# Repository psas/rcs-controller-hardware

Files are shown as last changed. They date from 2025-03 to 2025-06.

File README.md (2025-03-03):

# rcs-controller-hardware
The controller PCB for the RCS v2 module

Design documentation can be found [here](https://docs.google.com/document/d/1iXMG_Qmra7nCvFc8n4LBztUYELcxyuHCIxhkm7w4VaU/edit?usp=sharing).
## LICENSE

Copyright the Portland State Aerospace Society, 2025.

This source describes Open Hardware that is licensed under CERN-OHL-S v2, or any later version.

You may redistribute and modify this source and make products using it under the terms of the CERN-OHL-S v2 (https://ohwr.org/cern_ohl_s_v2.txt).

This source is distributed WITHOUT ANY EXPRESS OR IMPLIED WARRANTY, INCLUDING OF MERCHANTABILITY, SATISFACTORY QUALITY AND FITNESS FOR A PARTICULAR PURPOSE. Please see the CERN-OHL-S v2 for applicable conditions.

Source location: https://github.com/psas/

If you require a different license for this open hardware project, please contact us at [aerospace@pdx.edu](mailto:aerospace@pdx.edu).

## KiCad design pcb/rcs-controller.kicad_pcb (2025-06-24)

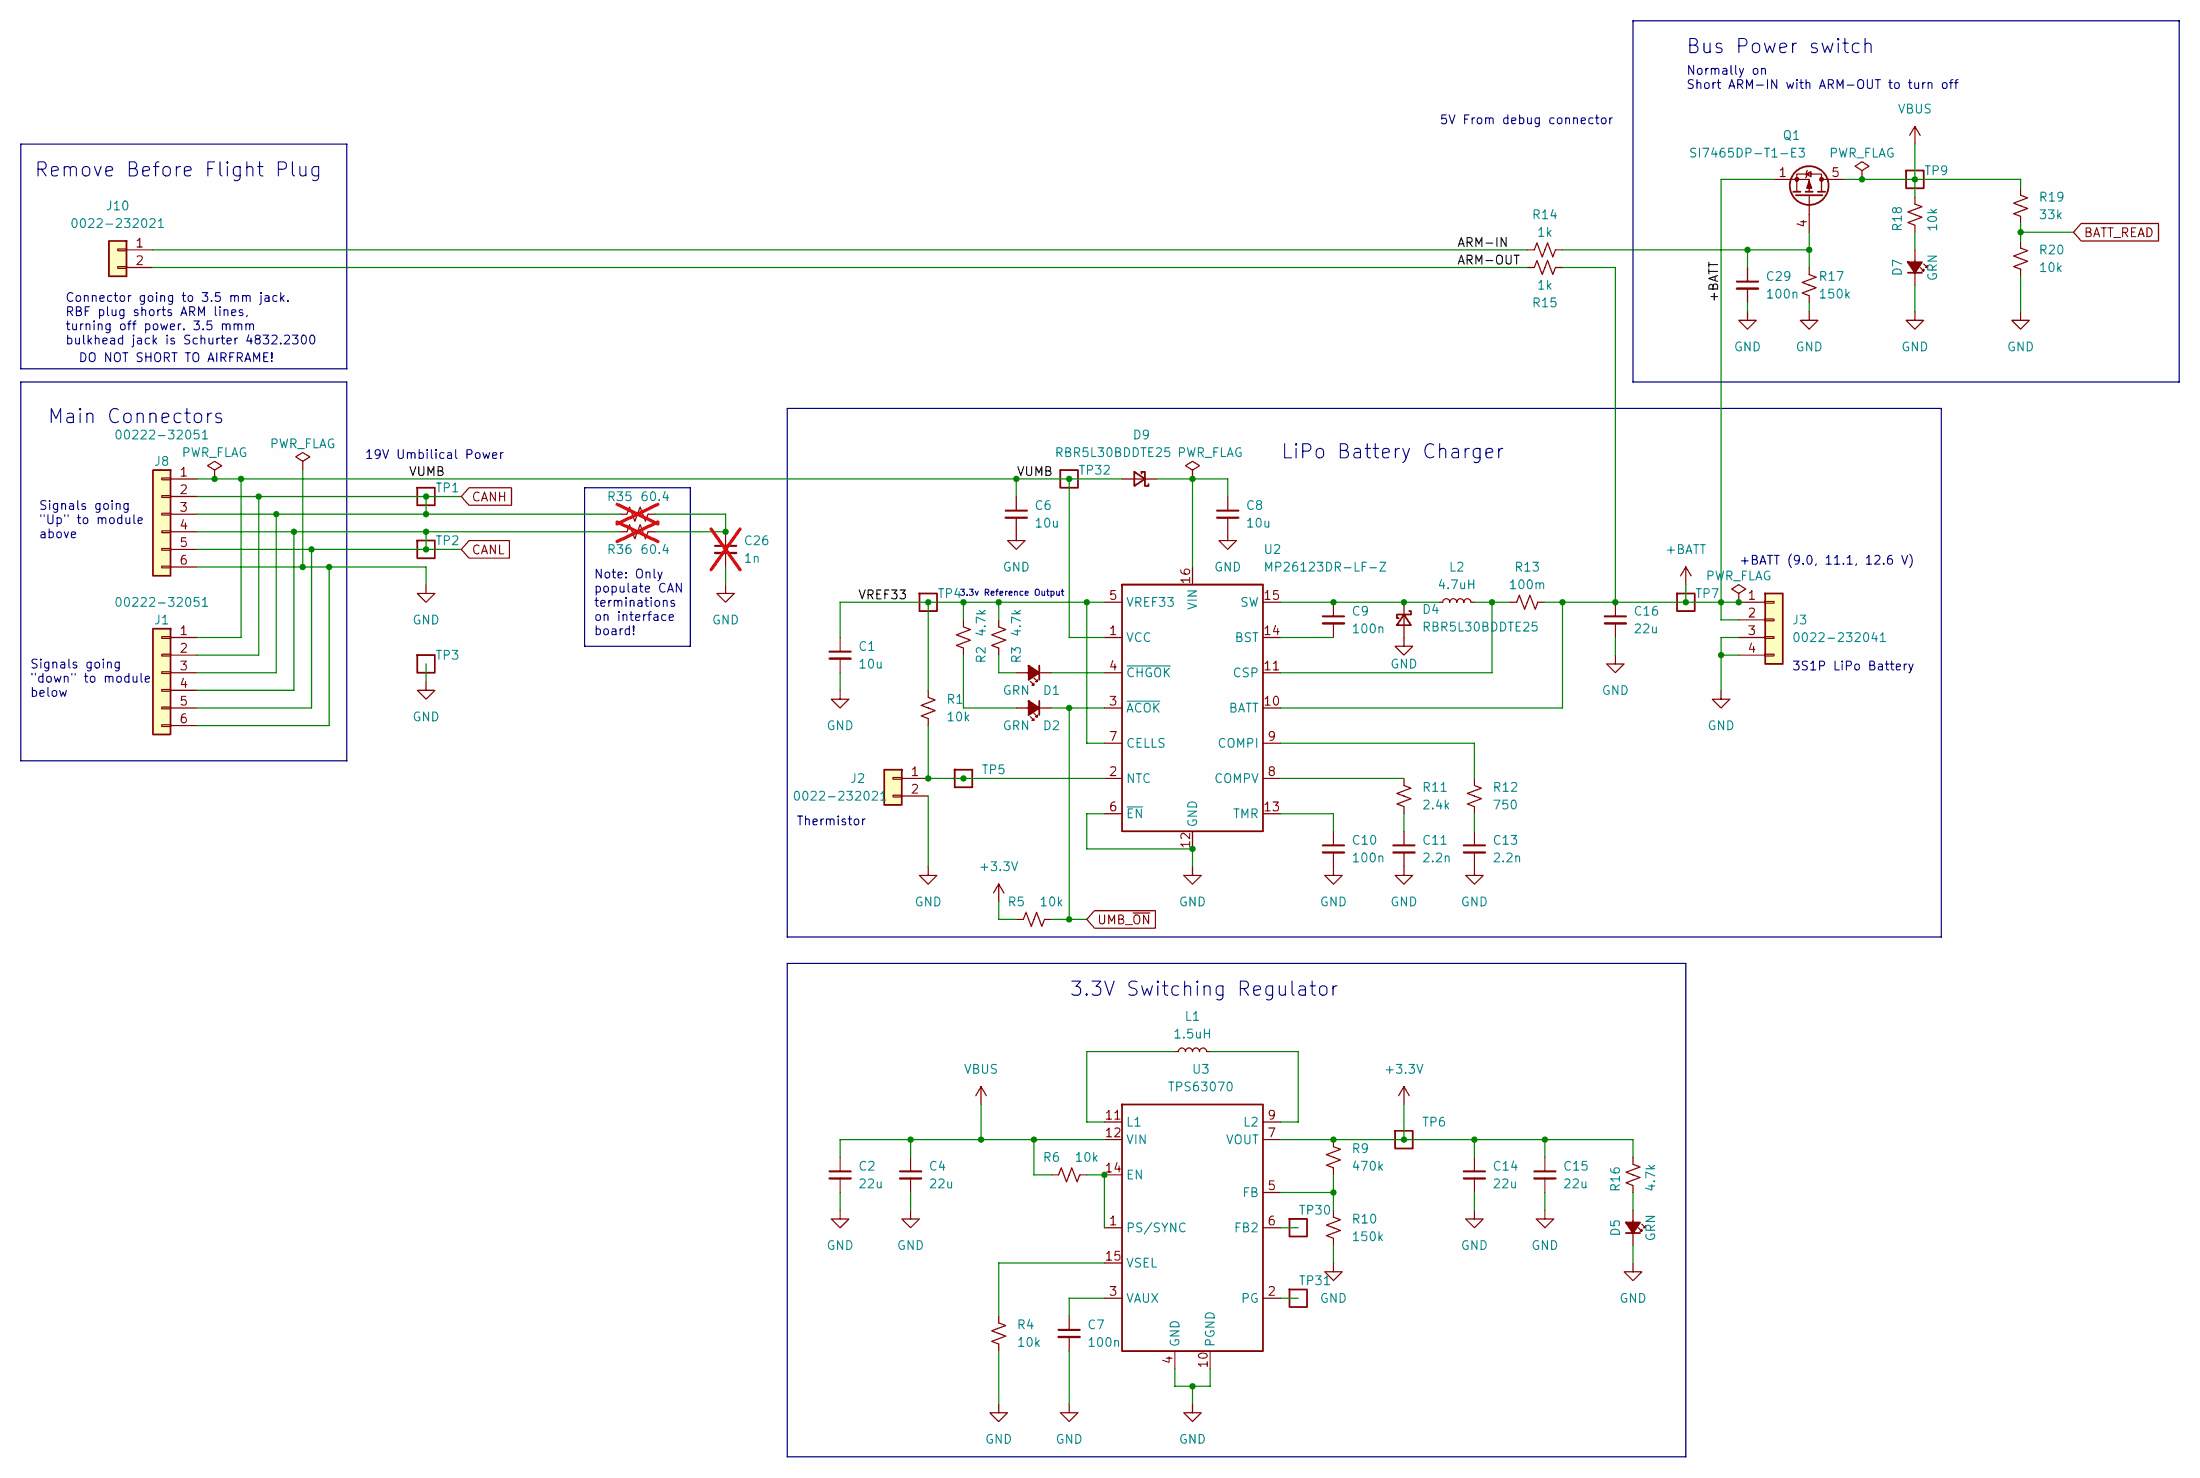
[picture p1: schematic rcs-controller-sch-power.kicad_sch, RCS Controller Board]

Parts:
C1, C6, C8: 10u; C_0805_2012Metric; MPN GRM21BR61H106KE43L
C2, C4, C14, C15, C16: 22u; C_0805_2012Metric; MPN C2012X5R1V226M125AC
C7, C9, C10, C29: 100n; C_0603_1608Metric; MPN CL10B104KB8WPNC
C11, C13: 2.2n; C_0603_1608Metric; MPN CL10B222KB8WPNC
C26: 1n; C_0603_1608Metric; MPN CL10B102KB85PNL; not fitted
D1, D2, D5, D7: GRN; LED_0603_1608Metric; MPN 150060GS75000
D4, D9: RBR5L30BDDTE25; D_SMA; MPN RBR5L30BDDTE25
J1, J8: 00222-32051; Molex_KK-254_AE-6410-06A_1x06_P2.54mm_Vertical; MPN 22232061
J2, J10: 0022-232021; Molex_KK-254_AE-6410-02A_1x02_P2.54mm_Vertical; MPN 22232021
J3: 0022-232041; Molex_KK-254_AE-6410-04A_1x04_P2.54mm_Vertical; MPN 22232041
L1: 1.5uH; L_Vishay_IHLP-2020; MPN IHLP2020CZER1R5M11
L2: 4.7uH; L_Vishay_IHLP-2020; MPN IHLP2020BZER4R7M11
Q1: SI7465DP-T1-E3; PowerPAK_SO-8_Single; MPN SI7141DP-T1-GE3
R1, R4, R5, R6, R18, R20: 10k; R_0603_1608Metric; MPN RC0603FR-0710KL
R2, R3, R16: 4.7k; R_0603_1608Metric; MPN RC0603FR-074K7L
R9: 470k; R_0603_1608Metric; MPN RC0603FR-07470KL
R10, R17: 150k; R_0603_1608Metric; MPN RC0603FR-07150KL
R11: 2.4k; R_0603_1608Metric; MPN RC0603FR-072K4L
R12: 750; R_0603_1608Metric; MPN RC0603FR-07750RL
R13: 100m; R_1206_3216Metric; MPN CSR1206FTR100
R14, R15: 1k; R_0603_1608Metric; MPN RC0603FR-071KL
R19: 33k; R_0603_1608Metric; MPN RC0603FR-0733KL
R35, R36: 60.4; R_1206_3216Metric; MPN RC0603FR-0760R4L; not fitted
TP1, TP2, TP3, TP4, TP5, TP6, TP7, TP9, TP30, TP31, TP32: Test-Point; TP-through-hole-1X01
U2: MP26123DR-LF-Z; QFN-16-1EP_4x4mm_P0.65mm_EP2.5x2.5mm; MPN MP26123DR-LF-Z
U3: TPS63070; U-TI-TPS63070; MPN TPS63070RNMR

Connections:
+3.3V: C14.1, C15.1, R5.1, R9.1, R16.1, TP6.1, U3.7 (VOUT), U3.8 (VOUT), U3.TIE2 (VOUT); also elsewhere on the board
+BATT: C16.1, J3.1, J3.2, Q1.1 (S), Q1.2 (S), Q1.3 (S), R13.2, R15.1, TP7.1, U2.10 (BATT)
/Power/ARM-IN: J10.1, R14.1
/Power/ARM-OUT: J10.2, R15.2
/Power/VREF33: C1.1, R1.1, R2.1, R3.1, TP4.1, U2.5 (VREF33), U2.7 (CELLS)
/Power/VUMB: C6.1, D9.2 (A), J1.1, J8.1, TP32.1, U2.1 (VCC)
BATT_READ: R19.2, R20.1; also elsewhere on the board
CANH: J1.2, J1.3, J8.2, J8.3, R35.1, TP1.1
CANL: J1.4, J1.5, J8.4, J8.5, R36.2, TP2.1
GND: C1.2, C2.2, C4.2, C6.2, C7.2, C8.2, C10.2, C11.2, C13.2, C14.2, C15.2, C16.2, C26.2, C29.2, D4.2 (A), D5.1 (K), D7.1 (K), J1.6, J2.2, J3.3, J3.4, J8.6, R4.2, R10.2, R17.2, R20.2, TP3.1, U2.6 (~EN), U2.12 (GND), U2.17 (GND), U3.4 (GND), U3.10 (PGND); also elsewhere on the board
unnamed: C11.1, R11.2
unnamed: C13.1, R12.2
unnamed: C26.1, R35.2, R36.1
unnamed: D1.2 (A), R3.2
unnamed: D1.1 (K), U2.4 (~CHGOK)
unnamed: D2.2 (A), R2.2
unnamed: C9.1, D4.1 (K), L2.1, U2.15 (SW)
unnamed: D5.2 (A), R16.2
unnamed: D7.2 (A), R18.2
unnamed: C8.1, D9.1 (K), U2.16 (VIN)
unnamed: J2.1, R1.2, TP5.1, U2.2 (NTC)
unnamed: C29.1, Q1.4 (G), R14.2, R17.1
unnamed: C9.2, U2.14 (BST)
unnamed: R12.1, U2.9 (COMPI)
unnamed: R11.1, U2.8 (COMPV)
unnamed: L2.2, R13.1, U2.11 (CSP)
unnamed: C10.1, U2.13 (TMR)
unnamed: R6.2, U3.1 (PS/SYNC), U3.14 (EN)
unnamed: TP30.1, U3.6 (FB2)
unnamed: R9.2, R10.1, U3.5 (FB)
unnamed: L1.1, U3.11 (L1)
unnamed: L1.2, U3.9 (L2)
unnamed: TP31.1, U3.2 (PG)
unnamed: C7.1, U3.3 (VAUX)
unnamed: R4.1, U3.15 (VSEL)
UMB_~ON: D2.1 (K), R5.2, U2.3 (~ACOK); also elsewhere on the board
VBUS: C2.1, C4.1, Q1.5 (D), R6.1, R18.1, R19.1, TP9.1, U3.12 (VIN), U3.13 (VIN), U3.TIE1 (VIN); also elsewhere on the board

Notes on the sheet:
LiPo Battery Charger
DO NOT SHORT TO AIRFRAME!
Thermistor
Signals going "down" to module below
Normally on Short ARM-IN with ARM-OUT to turn off
Connector going to 3.5 mm jack. RBF plug shorts ARM lines, turning off power. 3.5 mmm bulkhead jack is Schurter 4832.2300
Note: Only populate CAN terminations on interface board!
3S1P LiPo Battery
Signals going "Up" to module above
19V Umbilical Power
+BATT (9.0, 11.1, 12.6 V)
Bus Power switch
Main Connectors
3.3V Switching Regulator
5V From debug connector
3.3v Reference Output
Remove Before Flight Plug

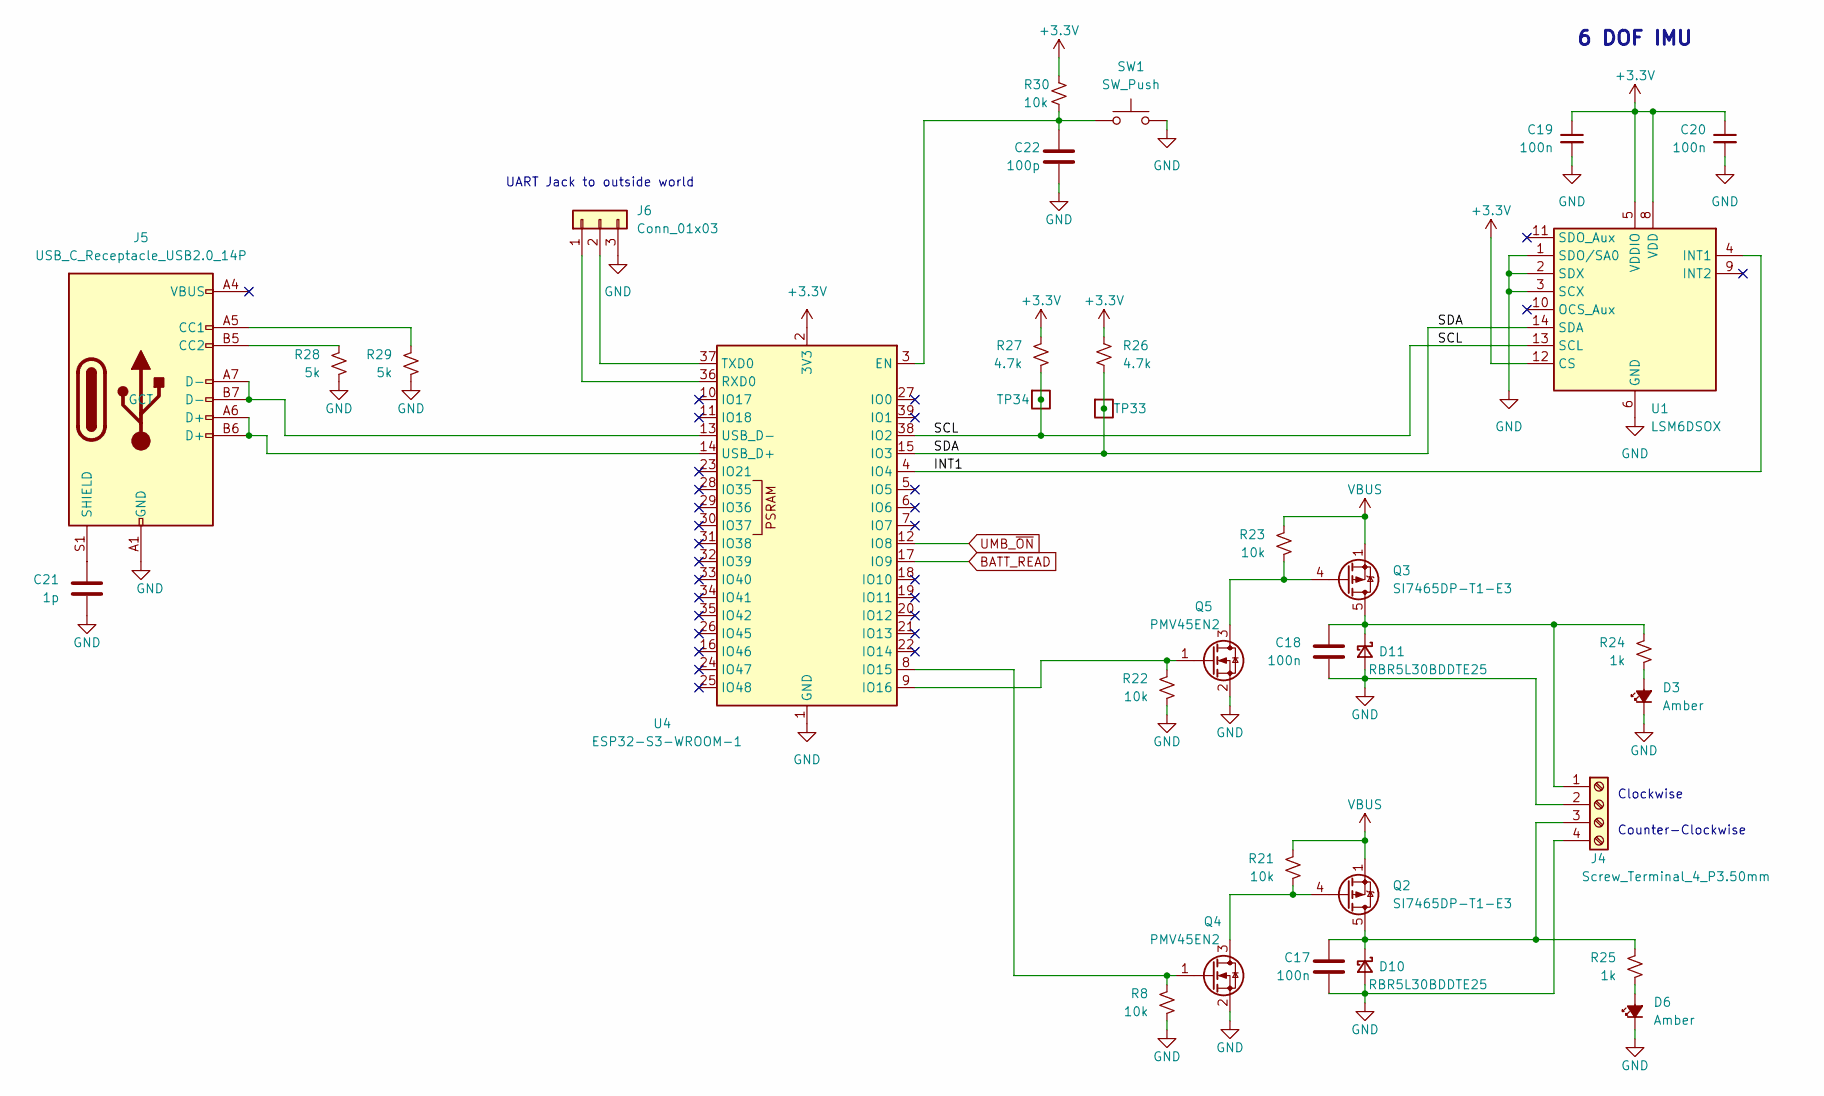
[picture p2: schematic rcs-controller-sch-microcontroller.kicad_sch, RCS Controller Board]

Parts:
C17, C18, C19, C20: 100n; C_0603_1608Metric; MPN CL10B104KB8WPNC
C21: 1p; C_0603_1608Metric; MPN CL10B104KB8WPNC
C22: 100p; C_0603_1608Metric; MPN CL10B104KB8WPNC
D3, D6: Amber; LED_0603_1608Metric; MPN 150060YS75000
D10, D11: RBR5L30BDDTE25; D_SMA; MPN RBR5L30BDDTE25
J4: Screw_Terminal_4_P3.50mm; TerminalBlock_Phoenix_PT-1,5-4-3.5-H_1x04_P3.50mm_Horizontal; MPN 1751264
J5: USB_C_Receptacle_USB2.0_14P; USB_C_Receptacle_Palconn_UTC16-G; MPN USB4105-GF-A
J6: Conn_01x03; PinHeader_1x03_P2.54mm_Vertical
Q2, Q3: SI7465DP-T1-E3; PowerPAK_SO-8_Single; MPN SI7141DP-T1-GE3
Q4, Q5: PMV45EN2; SOT-23-3; MPN PMV45EN2R
R8, R21, R22, R23, R30: 10k; R_0603_1608Metric; MPN RC0603FR-0710KL
R24, R25: 1k; R_0603_1608Metric; MPN RC0603FR-071KL
R26, R27: 4.7k; R_0603_1608Metric; MPN RC0603FR-074K7L
R28, R29: 5k; R_0603_1608Metric; MPN RC0603FR-0710KL
SW1: SW_Push; SW_PUSH_6mm; MPN B3F-1000
TP33, TP34: Test-Point; TP-through-hole-1X01
U1: LSM6DSOX; LGA-14_3x2.5mm_P0.5mm_LayoutBorder3x4y; MPN LSM6DSOXTR
U4: ESP32-S3-WROOM-1; MPN ESP32-S3-WROOM-1-N4R8

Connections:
+3.3V: C19.1, C20.1, R26.1, R27.1, R30.1, U1.5 (VDDIO), U1.8 (VDD), U1.12 (CS), U4.2 (3V3); also elsewhere on the board
/Microcontroller/INT1: U1.4 (INT1), U4.4 (IO4)
/Microcontroller/SCL: R27.2, TP34.1, U1.13 (SCL), U4.38 (IO2)
/Microcontroller/SDA: R26.2, TP33.1, U1.14 (SDA), U4.15 (IO3)
BATT_READ: U4.17 (IO9); also elsewhere on the board
GND: C17.2, C18.2, C19.2, C20.2, C21.2, C22.2, D3.1 (K), D6.1 (K), D10.2 (A), D11.2 (A), J4.2, J4.4, J5.A1 (GND), J5.A12 (GND), J5.B1 (GND), J5.B12 (GND), J6.3, Q4.2 (S), Q5.2 (S), R8.2, R22.2, R28.2, R29.2, SW1.2, U1.1 (SDO/SA0), U1.2 (SDX), U1.3 (SCX), U1.6 (GND), U1.7 (GND), U4.1 (GND), U4.40 (GND), U4.41 (GND); also elsewhere on the board
unnamed: D3.2 (A), R24.2
unnamed: D6.2 (A), R25.2
unnamed: C17.1, D10.1 (K), J4.3, Q2.5 (D), R25.1
unnamed: C18.1, D11.1 (K), J4.1, Q3.5 (D), R24.1
unnamed: J5.A5 (CC1), R29.1
unnamed: J5.B5 (CC2), R28.1
unnamed: C21.1, J5.S1 (SHIELD)
unnamed: J6.1, U4.36 (RXD0)
unnamed: J6.2, U4.37 (TXD0)
unnamed: Q2.4 (G), Q4.3 (D), R21.2
unnamed: Q3.4 (G), Q5.3 (D), R23.2
unnamed: Q4.1 (G), R8.1, U4.8 (IO15)
unnamed: Q5.1 (G), R22.1, U4.9 (IO16)
unnamed: C22.1, R30.2, SW1.1, U4.3 (EN)
unnamed: J5.A6 (D+), J5.B6 (D+), U4.14 (USB_D+)
unnamed: J5.A7 (D-), J5.B7 (D-), U4.13 (USB_D-)
UMB_~ON: U4.12 (IO8); also elsewhere on the board
VBUS: Q2.1 (S), Q2.2 (S), Q2.3 (S), Q3.1 (S), Q3.2 (S), Q3.3 (S), R21.1, R23.1; also elsewhere on the board

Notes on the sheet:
Counter-Clockwise
Clockwise
6 DOF IMU
UART Jack to outside world

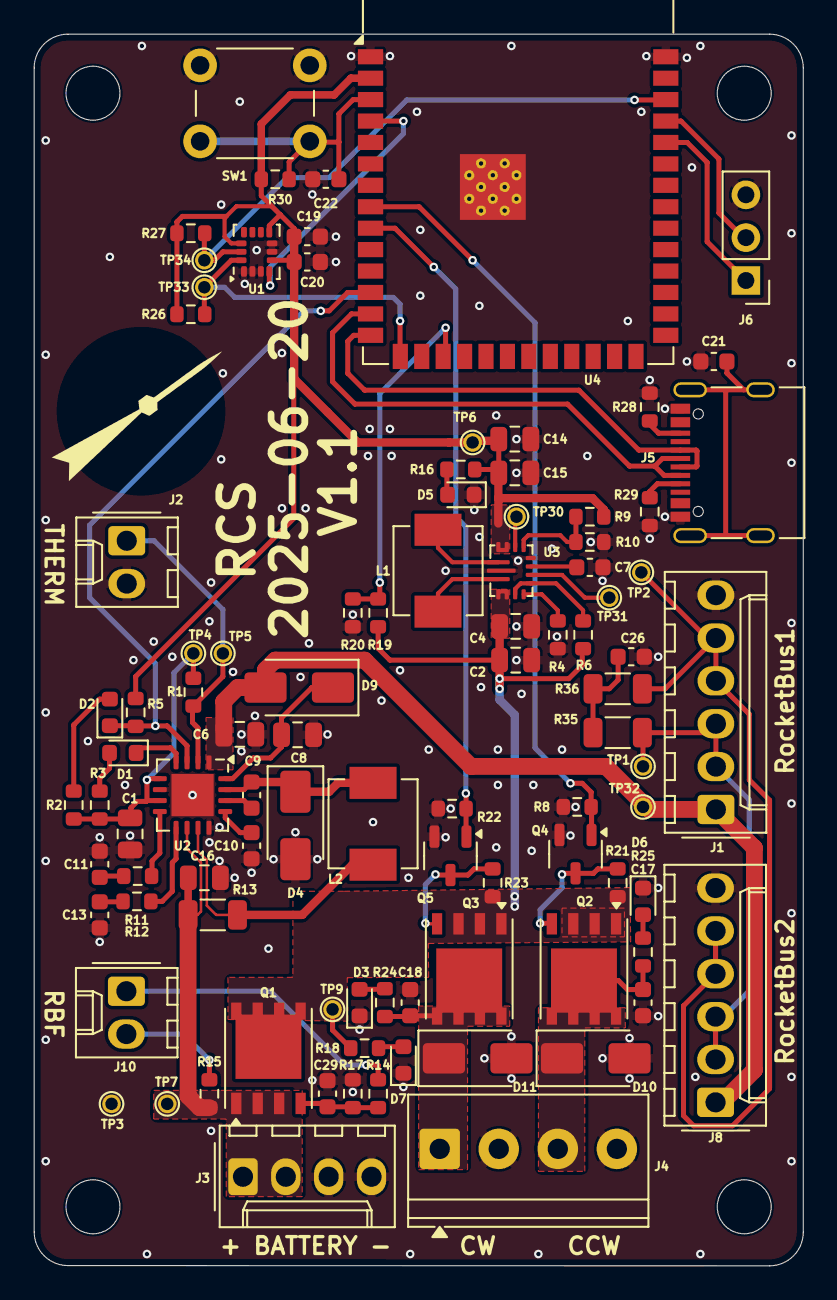
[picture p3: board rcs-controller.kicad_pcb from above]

Board: 2 copper layers, 45.6 x 73.0 mm, 96 parts (0 on the bottom side), 56 nets.

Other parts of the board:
LOGO1: PSAS_LOGO_10X10

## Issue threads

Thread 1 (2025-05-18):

3.3V SPS needs to be made 5V

jacoblikesblue, 2025-05-18:

andrewgreenberg, 2025-07-19:
No longer relevant on v1.2

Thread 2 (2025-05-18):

Feather footprint used it wrong

jacoblikesblue, 2025-05-18:

andrewgreenberg, 2025-07-19:
No longer relevant on v1.2

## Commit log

2025-03-10 first commit of kicad files
    [rcs-controller.kicad_pcb, rcs-controller.kicad_sch, untitled(1).kicad_sch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]
2025-03-24 Upload of rcs controller board 1st draft
    [rcs-controller.kicad_sch, untitled(1).kicad_sch, untitled.kicad_sch]
2025-03-31 Updated with footprint and more fleshed out circuit
    [rcs-controller.kicad_sch, untitled(1).kicad_sch, untitled.kicad_sch]
2025-04-02 Rough draft schematic, no ERC errors, ready for layout
    [untitled(1).kicad_sch, untitled.kicad_sch]
2025-04-02 remove temporary and lock files that were somehow committed; rename schematic files to something sane.
    [rcs-controller-sch-microcontroller.kicad_sch, rcs-controller-sch-power.kicad_sch, rcs-controller.kicad_sch]
2025-04-02 First circuit board
    [rcs-controller.kicad_pcb]
2025-04-10 Push to move to other machine
    [rcs-controller.kicad_pcb]
2025-04-24 Submit for review 4.23.2025
    [rcs-controller-sch-microcontroller.kicad_sch, rcs-controller-sch-power.kicad_sch, rcs-controller.kicad_pcb]
2025-04-25 Rev for review 4.25.2025
    [rcs-controller.kicad_pcb]
2025-04-28 Cleanup of Jacob's board; mostly ready for fab
    [rcs-controller.kicad_pcb]
2025-04-30 Fixed BOM, fixed missing symbol and footprint libraries, stitched vias, generated Gerbers.
    [rcs-controller-sch-microcontroller.kicad_sch, rcs-controller-sch-power.kicad_sch, rcs-controller.kicad_pcb]
2025-05-14 Added iBOM for easier board stuffing
2025-05-29 Rev 2.0
    Updated board with ESP32 chip to replace feather
    [rcs-controller-sch-microcontroller.kicad_sch, rcs-controller.kicad_pcb]
2025-06-03 Revision 6/2
    [rcs-controller-sch-microcontroller.kicad_sch, rcs-controller.kicad_pcb]
2025-06-04 Design review; fix schematic issues and some polish, some board to schematic patching, fix footprint issues.
    [rcs-controller-sch-microcontroller.kicad_sch, rcs-controller.kicad_pcb]
2025-06-16 Rev date 6.15
    [rcs-controller.kicad_pcb]
2025-06-16 rev date 6.16.2025
    [rcs-controller.kicad_pcb]
2025-06-18 Cleaner board
    [rcs-controller.kicad_pcb]
2025-06-18 Rev. 6.17
    [rcs-controller.kicad_pcb]
2025-06-19 Board design review; fix DRC errors. Back to Jacob for polishing.
    [rcs-controller.kicad_pcb]
2025-06-19 Silkscreen clean up
    [rcs-controller.kicad_pcb]
2025-06-20 More DRC cleanup, polishing, sticthing. Should be good to go.
    [rcs-controller.kicad_pcb]
2025-06-20 Oh, right, update the version and date.
    [rcs-controller.kicad_pcb, rcs-controller.kicad_sch]
2025-06-23 more polish, build Gerbers
    [rcs-controller.kicad_pcb]
2025-06-24 Push for design review 6.24
    [rcs-controller-sch-microcontroller.kicad_sch, rcs-controller-sch-power.kicad_sch, rcs-controller.kicad_pcb]
